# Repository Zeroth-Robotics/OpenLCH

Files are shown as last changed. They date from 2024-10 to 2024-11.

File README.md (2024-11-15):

<div align="center" style="text-align: center;">

  <h1>Zeroth Bot</h1>  (WIP)

<p> Super hackable, affordable, and end-to-end (sim2real, RL) 3D-printed open-source humanoid robot platform. Fully open-source, including hardware, SDK, and sim environments. BoM starts at $350. </p>

<p> This project is built by the open-source community and is currently work in progress. We welcome your feedback, issues, and pull requests in GitHub or joining our <a href="https://discord.gg/G6KP76uha5">Discord</a>. </p>

<h3>
  <a href="https://docs.zeroth.bot">Docs</a>
  <span> · </span>
  <a href="https://docs.zeroth.bot/roadmap">Roadmap</a>
  <span> · </span>
  <a href="https://discord.gg/G6KP76uha5">Contribute</a>
  <span> · </span>
  <a href="https://discord.gg/G6KP76uha5">Community</a>
</h3>

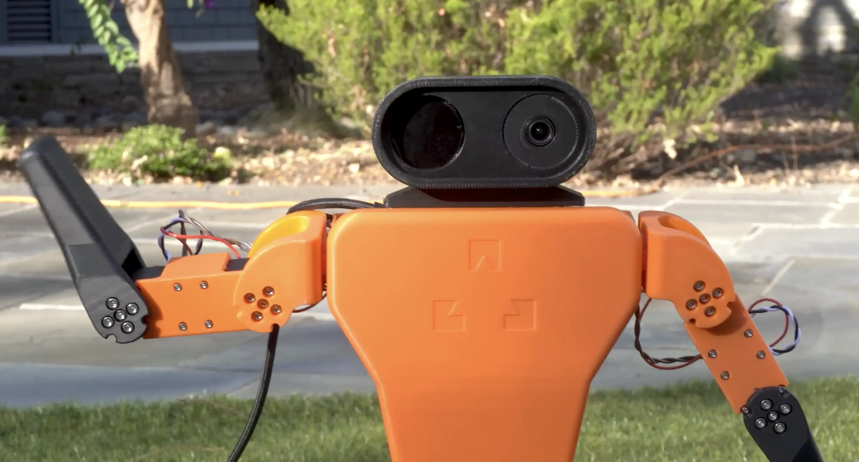
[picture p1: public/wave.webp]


</div>

---
### Project Status
Public Alpha. Zeroth-01 Bot is available for basic locomotion, vision, and speech, but expect breaking changes until 1.0 is reached.

### To start using Zeroth Bot
- Please see the Getting Started documentation at [https://docs.zeroth.bot](https://docs.zeroth.bot).

### To start developing Zeroth Bot
Zeroth Bot is developed by the open-source community. We welcome both pull requests and issues on GitHub.

- Join the community [Discord](https://discord.gg/G6KP76uha5)
- Documentation at [https://docs.zeroth.bot](https://docs.zeroth.bot)

### License
This project is licensed under the MIT License.

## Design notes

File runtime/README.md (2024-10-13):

# Runtime Documentation

## Setup

1. Flash the Image to the SD Card
Download the OpenLCH image from the [releases page](https://github.com/Zeroth-Robotics/OpenLCH-buildroot/releases).

Use Balena Etcher (or any other flashing tool) to flash the image onto your SD card.

Once flashing is complete, remove and reinsert the SD card into your computer.

3. Configure Wi-Fi on Startup
Open the boot folder on the SD card (it should be visible on macOS since it is formatted as FAT32).
Create a new file named wpa_supplicant.conf in the boot folder and add the following content:

```bash
ctrl_interface=/var/run/wpa_supplicant
ap_scan=1
update_config=1

network={
  ssid="YOURWIFINAME"
  psk="YOURPASSWORD"
  key_mgmt=WPA-PSK
}
```
Replace YOURWIFINAME and YOURPASSWORD with your Wi-Fi credentials.

3. Connect via USB
If you're connecting via USB, use the following details:

- IP Address: 192.168.42.1
- Username: root
- Password: milkv

SSH:
`ssh root@192.168.42.1`

4. Build Runtime
```bash
cargo check && gitlab-ci-local # check and build
```

5. Transfer Files to the Target Device
Find binaries in target/riscv64gc-unknown-linux-musl/release/

`scp -O target/riscv64gc-unknown-linux-musl/release/runtime $MILKV_IP:/usr/local/bin/`

Debug:
Note that you cannot ping the device in Cursor editor terminal for some reason. Try:
```bash
ping 192.168.42.1
```

6. Run the Application
To run the servo setup, execute the following on the target device:

```bash

# List available binaries
ls /usr/local/bin/

# Run your desired binary (example: runtime)
 /usr/local/bin/runtime
```

If the board is connected over usb, ip is `192.168.42.1`

---

## Architecture

Runtime Architecture

The goal of the runtime is to provide a unified interface for:

- robot configuration and declaration
- control loop execution
- state management
- model inference
- error handling and safety

## `config/[robot-name].toml`

Define the robot: joints, servos, parameters, etc.

Based on robot from `kscalelabs/firmware` config.

## `robot.rs`

Create the robot struct based on the config.toml file with all the servos and joints.

Provides the states for the robot.

Based on robot from `kscalelabs/firmware` Robot struct.

## `hal.rs`

Servo control code

## `controller.rs`

`StandingControllerPID` -> controller for standing using pre-set positions and PID controller

`StandingControllerPPO` -> controller for standing using PPO model

## `model.rs`

onnx inference session and initalization.

## `main.rs`

initialize config, robot, controller and start standing using controller.

# Hardware
Servo ID:


Wiring:


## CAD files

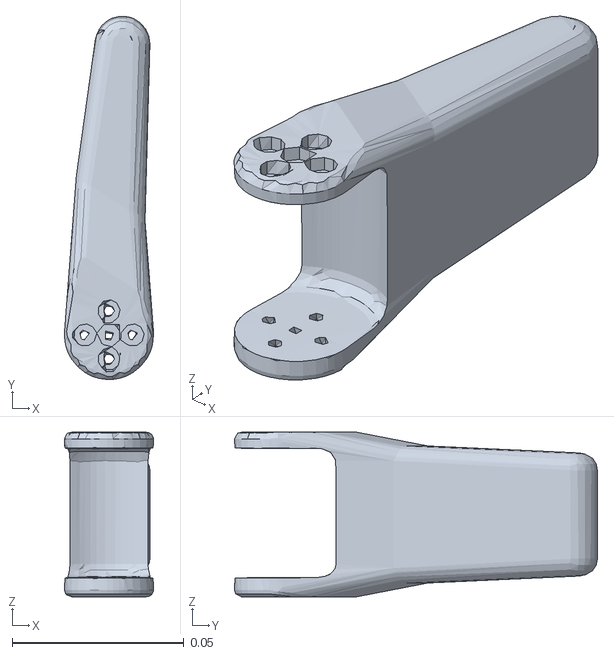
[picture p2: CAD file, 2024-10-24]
experiments/teleop/urdf/meshes/Left_Hand.stl
0.0259 x 0.106 x 0.048

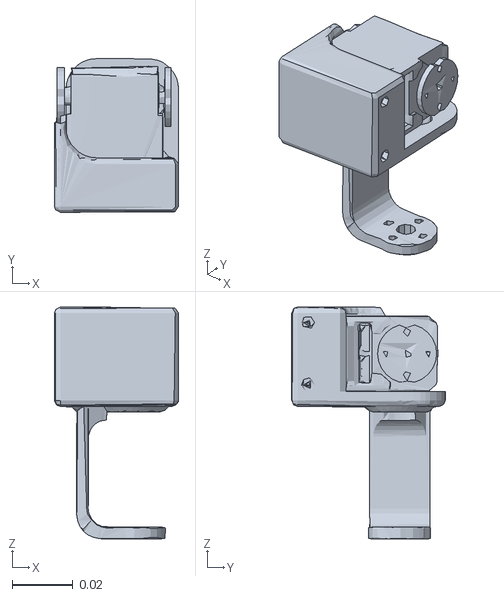
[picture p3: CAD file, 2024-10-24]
experiments/teleop/urdf/meshes/hip_yaw_right.stl
0.041 x 0.0507 x 0.0766

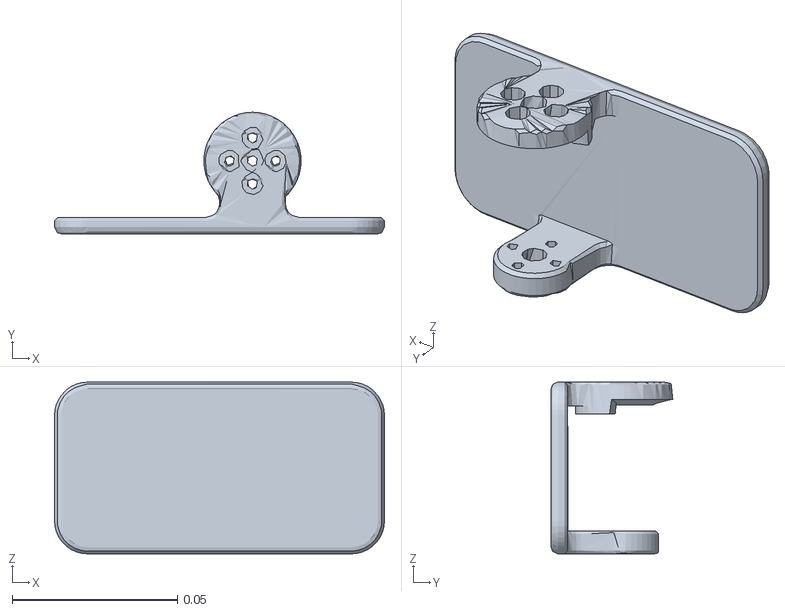
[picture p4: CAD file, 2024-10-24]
experiments/teleop/urdf/meshes/foot_right.stl
0.1 x 0.0369 x 0.0521

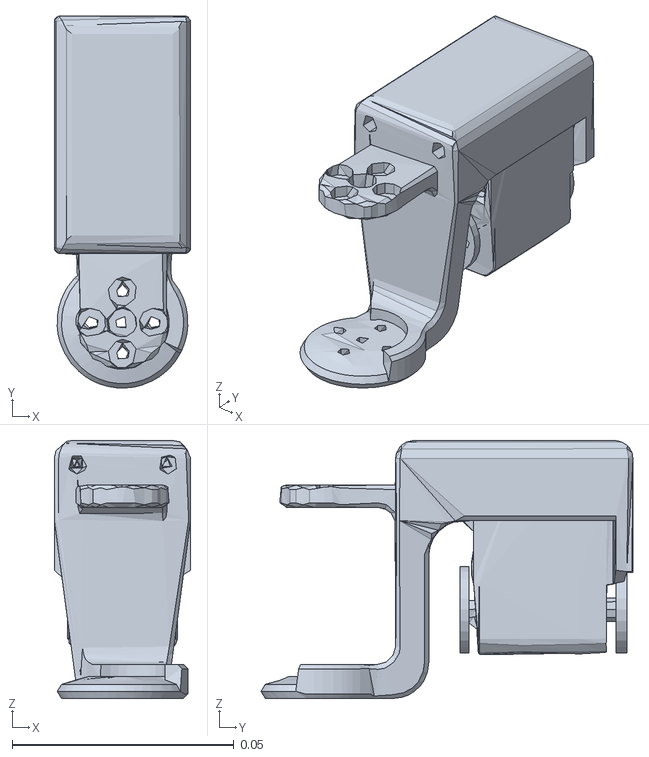
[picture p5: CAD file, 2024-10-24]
experiments/teleop/urdf/meshes/hip_roll_right.stl
0.0307 x 0.0838 x 0.0581

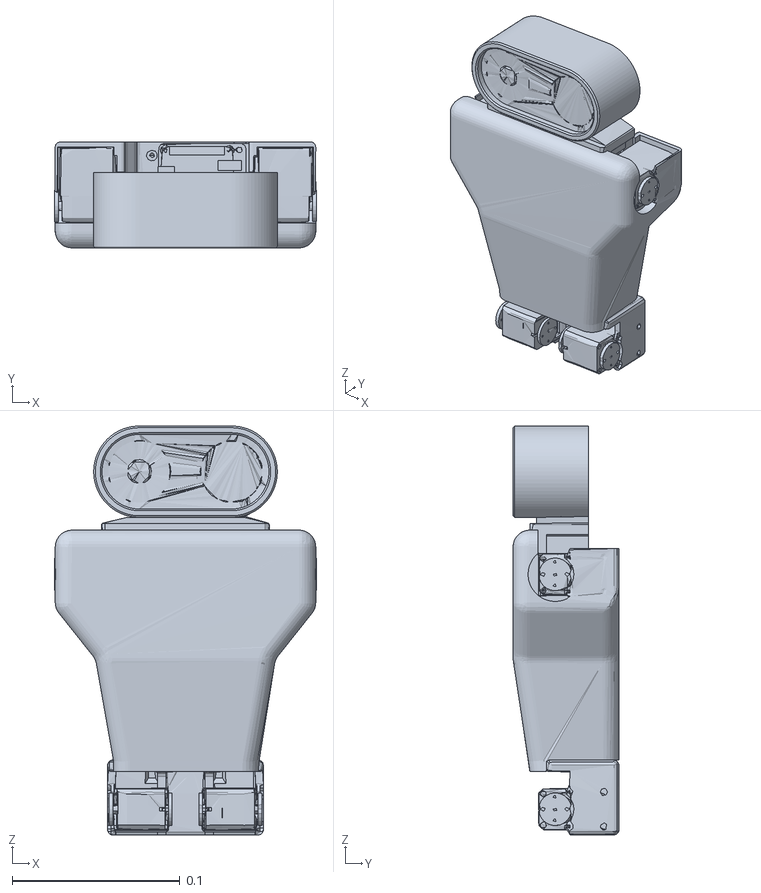
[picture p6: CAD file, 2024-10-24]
experiments/teleop/urdf/meshes/Torso.stl
0.156 x 0.0633 x 0.244

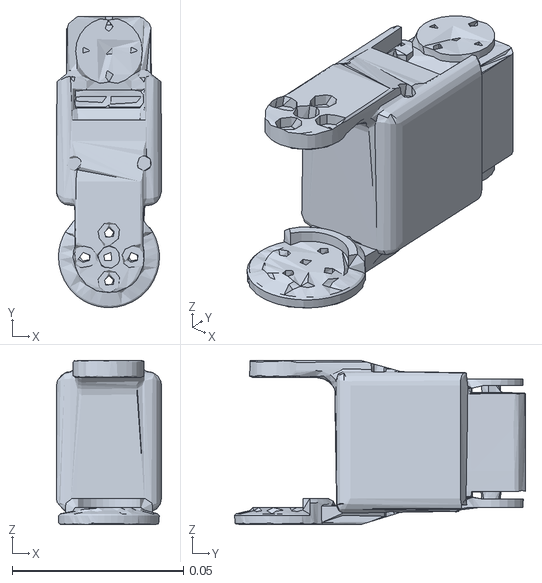
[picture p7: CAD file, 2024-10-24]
experiments/teleop/urdf/meshes/ankle_pitch_right.stl
0.0307 x 0.0851 x 0.048

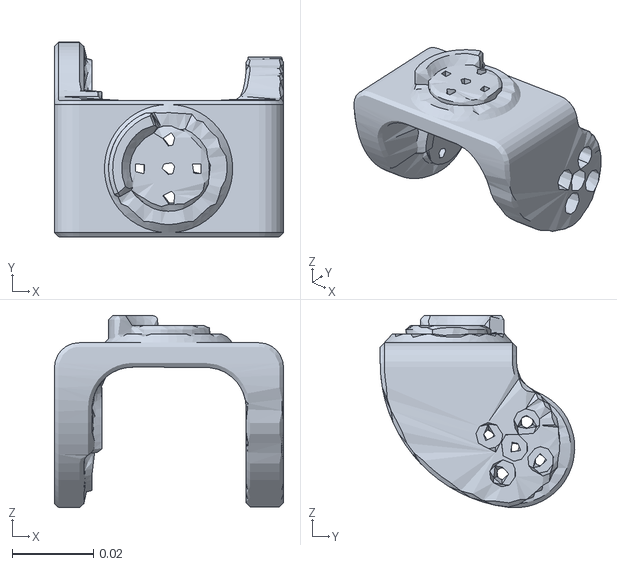
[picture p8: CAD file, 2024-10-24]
experiments/teleop/urdf/meshes/shoulder_yaw_left.stl
0.0562 x 0.0478 x 0.0472

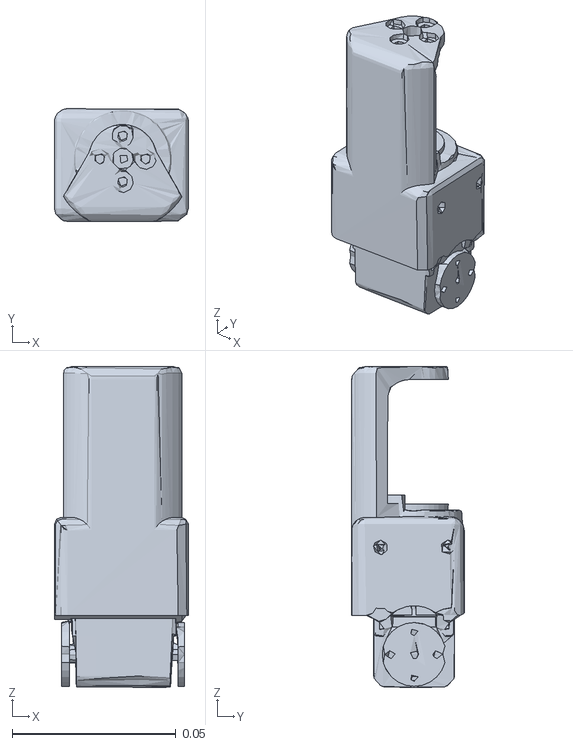
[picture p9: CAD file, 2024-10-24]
experiments/teleop/urdf/meshes/knee_pitch_right_2.stl
0.041 x 0.0345 x 0.0981

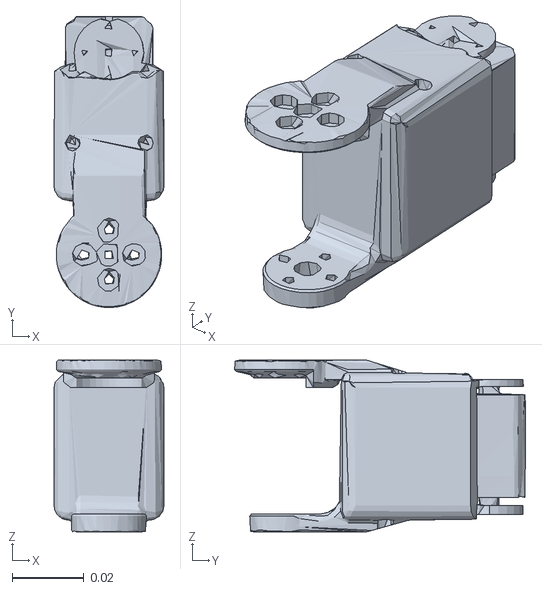
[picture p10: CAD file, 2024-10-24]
experiments/teleop/urdf/meshes/ankle_pitch_left.stl
0.0307 x 0.0813 x 0.048

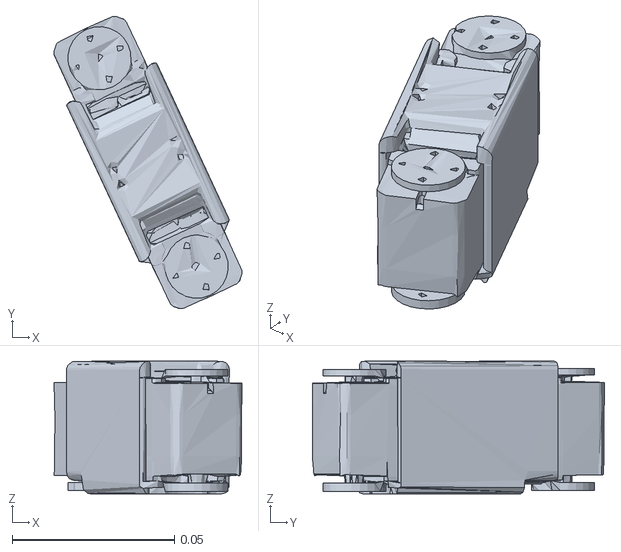
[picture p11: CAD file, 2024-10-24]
experiments/teleop/urdf/meshes/right_shoulder_yaw_motor.stl
0.058 x 0.0902 x 0.041

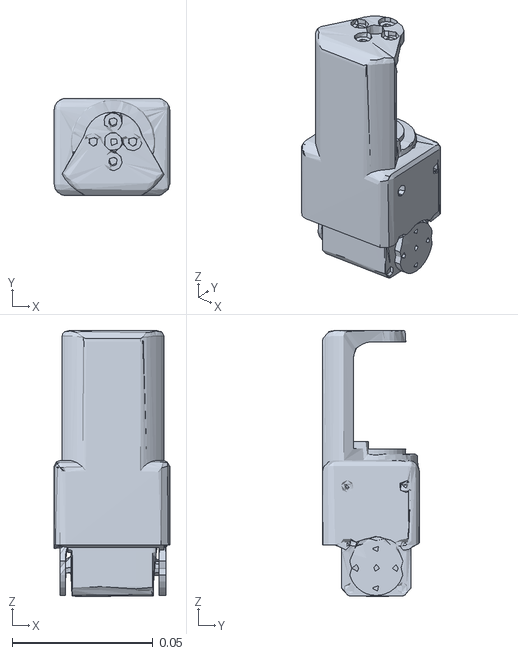
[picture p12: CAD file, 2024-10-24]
experiments/teleop/urdf/meshes/knee_pitch_right.stl
0.041 x 0.0345 x 0.0944

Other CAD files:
experiments/teleop/urdf/meshes/foot_left.stl
experiments/teleop/urdf/meshes/hip_roll_left.stl
experiments/teleop/urdf/meshes/hip_yaw_left.stl
experiments/teleop/urdf/meshes/hand_right.stl
experiments/teleop/urdf/meshes/shoulder_yaw_right.stl
experiments/teleop/urdf/meshes/left_shoulder_yaw_motor.stl

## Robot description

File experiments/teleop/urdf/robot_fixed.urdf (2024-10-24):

<robot name="opus">
  <link name="base">
    <inertial>
      <origin rpy="0 0 0" xyz="0 0 0" />
      <mass value="0.001" />
      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
    </inertial>
  </link>
  <joint name="floating_base" type="fixed">
    <origin rpy="0 0 0" xyz="0 0 0" />
    <parent link="base" />
    <child link="Torso" />
  </joint>
  <link name="Torso">
    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
    <inertial>
      <mass value="1.5697539312" />
      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
      <origin xyz="0.0006379977765356807 0.0037125891477163145 -0.0018039549717621631" rpy="0 0 0" />
    </inertial>
  </link>
  <joint name="right_shoulder_pitch" type="revolute">
    <origin xyz="-0.07813646375169968 -0.0003355559182753147 0.04305328991827533" rpy="1.5707963 2.220446049250313e-16 1.5707963" />
    <parent link="Torso" />
    <child link="shoulder_yaw_right" />
    <limit effort="1" velocity="20" lower="-1.5707963" upper="1.5707963" />
    <axis xyz="0 0 1" />
  </joint>
  <link name="shoulder_yaw_right">
    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
    <inertial>
      <mass value="0.040362728" />
      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
      <origin xyz="-0.00037600968 -0.0036566476 -0.017432914" rpy="0 0 0" />
    </inertial>
  </link>
  <joint name="left_shoulder_pitch" type="revolute">
    <origin xyz="0.0781635406483003 -0.0003355560817246521 0.04305329008172466" rpy="-1.5707963071795865 0.0 1.5707963000000003" />
    <parent link="Torso" />
    <child link="shoulder_yaw_left" />
    <limit effort="1" velocity="20" lower="-1.5707963" upper="1.5707963" />
    <axis xyz="0 0 1" />
  </joint>
  <link name="shoulder_yaw_left">
    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
    <inertial>
      <mass value="0.040363129" />
      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
      <origin xyz="-0.00037590896 0.0036565205 -0.017432695" rpy="0 0 0" />
    </inertial>
  </link>
  <joint name="right_shoulder_yaw" type="revolute">
    <origin xyz="-0.018825 -0.01629921 -0.03" rpy="3.1415927 -1.5707963 0" />
    <parent link="shoulder_yaw_right" />
    <child link="right_shoulder_yaw_motor" />
    <limit effort="1" velocity="20" lower="-1.5707963" upper="1.5707963" />
    <axis xyz="0 0 -1" />
  </joint>
  <link name="right_shoulder_yaw_motor">
    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
    <inertial>
      <mass value="0.17145988099999998" />
      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
      <origin xyz="-0.014954779548987598 0.03207058001285851 0.01810151127113155" rpy="0 0 0" />
    </inertial>
  </link>
  <joint name="right_hip_pitch" type="revolute">
    <origin xyz="-0.04563646320240432 -0.00033555485567163604 -0.09694671547403086" rpy="-1.570796353589792 -4.6410206566704915e-08 1.5707963000000003" />
    <parent link="Torso" />
    <child link="hip_yaw_right" />
    <limit effort="1" velocity="20" lower="-1.5707963" upper="1.5707963" />
    <axis xyz="0 0 -1" />
  </joint>
  <link name="hip_yaw_right">
    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
    <inertial>
      <mass value="0.10319577099999999" />
      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
      <origin xyz="-0.007775213144040673 -0.010188892005385952 0.015272495649744542" rpy="0 0 0" />
    </inertial>
  </link>
  <joint name="left_hip_pitch" type="revolute">
    <origin xyz="0.04566353964830031 -0.0003355550191209561 -0.09694671547403086" rpy="1.5707963535897942 -4.6410206566704915e-08 1.5707963000000003" />
    <parent link="Torso" />
    <child link="hip_yaw_left" />
    <limit effort="1" velocity="20" lower="-1.5707963" upper="1.5707963" />
    <axis xyz="0 0 -1" />
  </joint>
  <link name="hip_yaw_left">
    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
    <inertial>
      <mass value="0.103201904" />
      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
      <origin xyz="-0.007776157110492239 0.010188687432665504 0.015271760814946028" rpy="0 0 0" />
    </inertial>
  </link>
  <joint name="left_shoulder_yaw" type="revolute">
    <origin xyz="-0.018825 0.01629921 -0.03" rpy="3.1415927 1.5707963 0" />
    <parent link="shoulder_yaw_left" />
    <child link="left_shoulder_yaw_motor" />
    <limit effort="1" velocity="20" lower="-1.5707963" upper="1.5707963" />
    <axis xyz="0 0 1" />
  </joint>
  <link name="left_shoulder_yaw_motor">
    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
    <inertial>
      <mass value="0.171459652" />
      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
      <origin xyz="0.01495475586438801 -0.03207058301892832 -0.018101540546377845" rpy="0 0 0" />
    </inertial>
  </link>
  <joint name="right_hip_yaw" type="revolute">
    <origin xyz="-0.02550000162875169 0.0025000011415515153 0.019359999918275368" rpy="9.282041333256968e-08 1.5707963000000005 0.0" />
    <parent link="hip_yaw_right" />
    <child link="hip_roll_right" />
    <limit effort="1" velocity="20" lower="-0.087266463" upper="1.5707963" />
    <axis xyz="0 0 1" />
  </joint>
  <link name="hip_roll_right">
    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
    <inertial>
      <mass value="0.111293388" />
      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
      <origin xyz="5.2211227247596255e-05 0.04271834544407224 0.027962543113983985" rpy="0 0 0" />
    </inertial>
  </link>
  <joint name="left_hip_yaw" type="revolute">
    <origin xyz="-0.02550000297464769 -0.0025000010000000017 0.01936000008172467" rpy="-3.1415926071795863 -1.5707963 0.0" />
    <parent link="hip_yaw_left" />
    <child link="hip_roll_left" />
    <limit effort="1" velocity="20" lower="-1.5707963" upper="0.087266463" />
    <axis xyz="0 0 1" />
  </joint>
  <link name="hip_roll_left">
    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
    <inertial>
      <mass value="0.111293526" />
      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
      <origin xyz="-5.2212826152564546e-05 0.04271835909112089 0.027962565619545642" rpy="0 0 0" />
    </inertial>
  </link>
  <joint name="right_elbow_yaw" type="revolute">
    <origin xyz="-0.03000311610855749 0.06434189253104221 0.00025000101875458525" rpy="8.847213864293657e-08 -1.9613800805728943e-08 0.4363323099999996" />
    <parent link="right_shoulder_yaw_motor" />
    <child link="Left_Hand" />
    <limit effort="1" velocity="20" lower="-1.2217305" upper="1.2217305" />
    <axis xyz="0 0 1" />
  </joint>
  <link name="Left_Hand">
    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
    <inertial>
      <mass value="0.075184887" />
      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
      <origin xyz="0.0011184952 0.046132358 0.018254412" rpy="0 0 0" />
    </inertial>
  </link>
  <joint name="left_elbow_yaw" type="revolute">
    <origin xyz="0.03000311710160605 -0.06434189183411612 -0.0002500013458960012" rpy="-3.141592607179586 -2.220446049250313e-16 0.43633231000000006" />
    <parent link="left_shoulder_yaw_motor" />
    <child link="hand_right" />
    <limit effort="1" velocity="20" lower="-1.2217305" upper="1.2217305" />
    <axis xyz="0 0 1" />
  </joint>
  <link name="hand_right">
    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
    <inertial>
      <mass value="0.075183656" />
      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
      <origin xyz="-0.0011185716 0.046132566 0.018254616" rpy="0 0 0" />
    </inertial>
  </link>
  <joint name="right_hip_roll" type="revolute">
    <origin xyz="0.0 0.06776001387753285 0.015000000939161373" rpy="1.5707963999999996 0.0 0.0" />
    <parent link="hip_roll_right" />
    <child link="knee_pitch_right" />
    <limit effort="1" velocity="20" lower="-0.78539816" upper="0.78539816" />
    <axis xyz="0 0 1" />
  </joint>
  <link name="knee_pitch_right">
    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
    <inertial>
      <mass value="0.11061241299999999" />
      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
      <origin xyz="0.0007189519537218518 -0.0023746643916922137 -0.021913106490424647" rpy="0 0 0" />
    </inertial>
  </link>
  <joint name="left_hip_roll" type="revolute">
    <origin xyz="0.0 0.06776001212246713 0.014999999060838654" rpy="1.5707963 0.0 0.0" />
    <parent link="hip_roll_left" />
    <child link="knee_pitch_right_2" />
    <limit effort="1" velocity="20" lower="-0.78539816" upper="0.78539816" />
    <axis xyz="0 0 1" />
  </joint>
  <link name="knee_pitch_right_2">
    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
    <inertial>
      <mass value="0.11061241299999999" />
      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
      <origin xyz="-0.0006438206184322414 -0.0023746644421732206 -0.024438821233669406" rpy="0 0 0" />
    </inertial>
  </link>
  <joint name="right_knee_pitch" type="revolute">
    <origin xyz="0.01882501239711481 -9.39161338975314e-10 -0.04221000153916135" rpy="-1.5707963 0.0 1.5707963" />
    <parent link="knee_pitch_right" />
    <child link="ankle_pitch_right" />
    <limit effort="1" velocity="20" lower="-1.0471976" upper="1.0471976" />
    <axis xyz="0 0 1" />
  </joint>
  <link name="ankle_pitch_right">
    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
    <inertial>
      <mass value="0.109625116" />
      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
      <origin xyz="-5.290268857115649e-07 0.04092239693101483 0.017864163896558594" rpy="0 0 0" />
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

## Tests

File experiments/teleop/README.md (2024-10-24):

# Teleop (WIP)

Documentation link: https://docs.zeroth.bot/software/teleop

Objective: Control the robot using a GUI by setting target positions for the hands or using VR controllers.

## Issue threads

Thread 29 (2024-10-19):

python lib set_positions sets all the positions, not just the specified one

npfoss, 2024-10-19:
using this function as a wrapper fixes it, but the underlying bug is in the rust code (never updates `last_positions`, we think?)

```py
def set_one(id, position):
    current_pos = hal.servo.get_positions()
    updated_pos = [(servo_id, position if servo_id == id else pos) for servo_id, pos in current_pos]
    print('setting', updated_pos)
    hal.servo.set_positions(updated_pos)
```

hatomist, 2024-10-22:
should be fixed by
https://github.com/Zeroth-Robotics/OpenLCH/commit/ddc89fab7815edb4a0c2348b4526b904a46f3129

Closed 2024-10-22.

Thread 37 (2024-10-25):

Fix `openlch start-calibration #` id setting permanence

jingxiangmo, 2024-10-25:
Currently not consistent

hatomist, 2024-10-29:
should be fixed by v0.2.3 of image

Closed 2024-10-29.

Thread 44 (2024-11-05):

Calibration doesn't save min/max results

jingxiangmo, 2024-11-05:

jingxiangmo, 2024-11-05:
issue noted two days ago. After setting the robot to calibrate, the calibrated value didn't save.

Closed 2024-11-08.

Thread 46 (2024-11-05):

Sending all servos to 0s after calibration issue

jingxiangmo, 2024-11-05:
Change cables?

jingxiangmo, 2024-11-05:
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

Closed 2024-11-08.

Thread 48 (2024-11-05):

Electromagnetic interference (EMI) from cables to servo

jingxiangmo, 2024-11-05:
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

jingxiangmo, 2024-11-05:
i suspect it's the longer cables. can we can new cables made in China or etc. EMI would mess with the policy input

Closed 2024-11-08.

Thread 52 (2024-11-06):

openlch 0.9.0 issues

jingxiangmo, 2024-11-06:

jingxiangmo, 2024-11-07:
- `openlch set-position [joint id] [position]` does not set servo positions
- read_servos_id missing #16

jingxiangmo, 2024-11-07:
```
(openlch) ➜  inference git:(walked) ✗ openlch scan-servos
Found servo IDs:
1
2
3
4
5
6
7
8
9
10
11
12
13
14
15
(openlch) ➜  inference git:(walked) ✗ openlch set-position 16 40
```

Closed 2024-11-08.

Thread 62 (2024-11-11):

Add visual command arrow to sim visualization

henri123lemoine, 2024-11-11:
The simulation needs a visual indicator (green arrow) showing the commanded direction/velocity of the robot. E.g. visual linear velocity commands (x,y) and angular velocity/heading commands.

henri123lemoine, 2024-11-11:
(wrong repo)

henri123lemoine, 2024-11-11:
(wrong repo)

henri123lemoine, 2024-11-11:
(wrong repo)

Closed 2024-11-11.

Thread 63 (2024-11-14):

`start-calibration` doesn't start unless cancel first with new image

jingxiangmo, 2024-11-14:

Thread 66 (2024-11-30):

Does zeroth-bot have gazebo emulation robots,Thinks.

runkezhong, 2024-11-30:

jingxiangmo, 2024-11-30:
The bot has a URDF  file that defines link and joints (, which we use in Isaac Gym. You can convert the URDF to SDF (Gazebo compatible format) using a converter like `gz sdf`

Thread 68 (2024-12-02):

Switch submodule connection from SSH to HTTPS

henri123lemoine, 2024-12-02:
In `.gitmodules`, "sim" submodule URL switch from `git@github.com:Zeroth-Robotics/sim.git` to `https://github.com/zeroth-robotics/sim.git`. I'm not entirely sure that would fix the issue with `--recurse-submodules` cloning of zeroth-bot, but don't see why it wouldn't.

Closed 2025-05-24.

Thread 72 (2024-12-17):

The price of sts3250 is actually 80.15

GoingMyWay, 2024-12-17:
https://www.aliexpress.us/item/3256806337383027.html?gatewayAdapt=glo2usa4itemAdapt

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

The price of sts3250 is actually 80.15

On Taobao.com the price is RMB 464.

lijiajun3029, 2024-12-25:
I think this is very expensive.

jingxiangmo, 2024-12-25:
Yeah the seller has significantly increased the cost of STS3250s... We're getting new custom STS3215s with high RPMs made right now

GoingMyWay, 2024-12-26:
> Yeah the seller has significantly increased the cost of STS3250s... We're getting new custom STS3215s with high RPMs made right now

Do you mean the price of it was low?

jingxiangmo, 2024-12-26:
Yup, 3215 was $11 and 3250 was $30. We originally started with 3215, but 3250's performance was better because of the higher RPM so we changed the BoM for 3250 as we're getting custom servos made by new suppliers right now that would be 3215 price but 65 RPM

lijiajun3029, 2024-12-27:
> Yup, 3215 was $11 and 3250 was $30. We originally started with 3215, but 3250's performance was better because of the higher RPM so we changed the BoM for 3250 as we're getting custom servos made by new suppliers right now that would be 3215 price but 65 RPM

Further consider how much torque and rpm we need in different parts(legs and hands) of the robot？some sts3215 have 19.5kg@7.4v torque and 52rpm@7.4v(but our battery is 12v)

Closed 2024-12-25.

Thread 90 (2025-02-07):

Something wrong with environmental issues and a value bug of run.py

BitBelief, 2025-02-07:
**wrong message:**
(humanoid-os) **user@user-System-Product-Name:~/zeroth-bot$** python experiments/run.py
pygame 2.6.1 (SDL 2.28.4, Python 3.12.8)
Hello from the pygame community. https://www.pygame.org/contribute.html
INFO:robot:Robot initializing...
INFO:robot:Checking connection to robot...
INFO:robot:Successfully pinged robot.
INFO:robot:Scanning servos...
Error during robot operation: <_InactiveRpcError of RPC that terminated with:
	status = StatusCode.UNIMPLEMENTED
	details = ""
	debug_error_string = "UNKNOWN:Error received from peer  {grpc_message:"", grpc_status:12, created_time:"2025-02-06T17:10:41.2711877+08:00"}"
>
Traceback (most recent call last):
  File "/home/user/zeroth-bot/experiments/run.py", line 478, in <module>
    main()
  File "/home/user/zeroth-bot/experiments/run.py", line 468, in main
    stop_event.set()
    ^^^^^^^^^^
UnboundLocalError: cannot access local variable 'stop_event' where it is not associated with a value

**anotherone(about video-stream service):**
(humanoid-os) <font color="#4E9A06"><b>user@user-System-Product-Name</b></font>:<font color="#3465A4"><b>~/zeroth-bot</b></font>$ openlch start-video-stream
An error occurred: <_InactiveRpcError of RPC that terminated with:
	status = StatusCode.UNIMPLEMENTED
	details = ""
	debug_error_string = "UNKNOWN:Error received from peer  {grpc_message:"", grpc_status:12, created_time:"2025-02-06T17:10:18.204871362+08:00"}"
>

mrking66, 2025-03-22:
hey,have you been solved this problem?I have the same problem,too.It seems to be a gRPC error, and I'm not sure if the server has implemented the method called by the client.

BitBelief, 2025-04-11:
I'm sorry to tell you that I still haven't found a solution.If I find a solution I will leave a message on it.

Closed 2025-05-24.

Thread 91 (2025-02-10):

Docs don't show how to initialize the robot

fruit-lxe, 2025-02-10:
How to initialize the robot to ensure that it is in the same position every time it is powered on, so that subsequent actions can be performed?

Mysticwaan, 2025-03-09:
Use a limit switch, encoder, or preset servo position to the robot on startup @fruit-lxe

jingxiangmo, 2025-03-15:
There's a calibration script that goes to max and minimum positions, and then the zero position is the half

jingxiangmo, 2025-03-15:
Thanks, I will update the docs

Closed 2025-05-24.

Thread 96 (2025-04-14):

The link in the "ID and calibration" has expired.

Kyaru-Momochi, 2025-04-14:
It show me error code: 502

Closed 2025-05-24.

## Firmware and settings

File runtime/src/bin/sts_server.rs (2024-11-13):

use tonic::{transport::Server, Request, Response, Status};
use tower_http::cors::CorsLayer;
use std::sync::Arc;
use tokio::sync::Mutex;
use anyhow::Result;
use std::fs::File;
use std::io::Write;
use std::path::Path;
use std::process::{Command, Stdio};
use std::net::IpAddr;
use regex::Regex;
use std::sync::atomic::{AtomicBool, Ordering};
use tokio::task;
use std::time::Duration;
use std::env;
use runtime::hal::{Servo, IMU, MAX_SERVOS, ServoMultipleWriteCommand, ServoData, ServoMode, ServoDirection, ServoRegister, TorqueMode};
use std::collections::HashMap;
use tokio::sync::RwLock;
use uuid::Uuid;
use tokio::fs;
use std::path::PathBuf;
use std::pin::Pin;
use chrono::prelude::*;
use tokio_stream::{self, StreamExt, Stream};

pub mod servo_control {
    tonic::include_proto!("hal_pb");
}

use servo_control::servo_control_server::{ServoControl, ServoControlServer};
use servo_control::{Empty, JointPositions, WifiCredentials, ServoId, ServoInfo, ServoIds, IdChange, ChangeIdResponse, ServoInfoResponse, servo_info_response, change_id_response, VideoStreamUrls, CalibrationResponse, CalibrationStatus, TorqueSettings, TorqueEnableSettings, ImuData, Vector3, AudioChunk, UploadResponse, PlayRequest, RecordingConfig, CalibrationRequest};

#[derive(Debug)]
pub struct StsServoControl {
    servo: Arc<Mutex<Servo>>,
    imu: Arc<Mutex<Option<IMU>>>,
    last_positions: Arc<Mutex<ServoData>>,
    calibrating_servo: Arc<Mutex<Option<u8>>>,
    calibration_running: Arc<AtomicBool>,
    audio_files: Arc<RwLock<HashMap<String, PathBuf>>>,
    recording_running: Arc<AtomicBool>,
}

impl StsServoControl {
    pub fn new() -> Result<Self> {
        let servo = Servo::new()?;
        let imu = IMU::new().ok();
        servo.enable_readout()?;
        let initial_data = servo.read_continuous()?;
        
        Ok(Self {
            servo: Arc::new(Mutex::new(servo)),
            imu: Arc::new(Mutex::new(imu)),
            last_positions: Arc::new(Mutex::new(initial_data)),
            calibrating_servo: Arc::new(Mutex::new(None)),
            calibration_running: Arc::new(AtomicBool::new(false)),
            audio_files: Arc::new(RwLock::new(HashMap::new())),
            recording_running: Arc::new(AtomicBool::new(false)),
        })
    }

    fn get_interface_ip(interface: &str) -> Option<IpAddr> {
        let output = Command::new("ip")
            .args(&["addr", "show", interface])
            .output()
            .ok()?;
        
        let output_str = String::from_utf8_lossy(&output.stdout);
        let ip_regex = Regex::new(r"inet\s+(\d+\.\d+\.\d+\.\d+)").ok()?;
        
        ip_regex.captures(&output_str)
            .and_then(|cap| cap.get(1))
            .and_then(|m| m.as_str().parse().ok())
    }

    async fn calibrate_servo(&self, servo_id: u8, calibration_speed: u16, current_threshold: f32) -> Result<(), Status> {
        let servo = self.servo.clone();
        let calibrating_servo = self.calibrating_servo.clone();
        let calibration_running = self.calibration_running.clone();

        task::spawn(async move {
            let servo = servo.lock().await;

            servo.disable_movement().unwrap();


            servo.disable_readout().unwrap();
            servo.set_mode(servo_id, ServoMode::ConstantSpeed).unwrap();

            servo.write_servo_memory(servo_id, runtime::hal::ServoRegister::TorqueLimit, 150).unwrap();

            let mut max_forward = 0;
            let mut max_backward = 0;

            let version = servo.read(servo_id, ServoRegister::ServoMainVersion, 2).unwrap();
            let mut current_multiplier = 1.0;

            // sts3215
            if version[0] == 0x09 && version[1] == 0x03 {
                current_multiplier = 6.5;
            }

            for pass in 0..2 {
                let direction = if pass == 0 { ServoDirection::Clockwise } else { ServoDirection::Counterclockwise };
                servo.set_speed(servo_id, calibration_speed, direction).unwrap();

                let mut threshold_exceeded_count = 0;

                loop {
                    if !calibration_running.load(Ordering::SeqCst) {
                        servo.set_speed(servo_id, 0, ServoDirection::Clockwise).unwrap();
                        return;
                    }

                    let mut info = servo.read_info(servo_id).unwrap();
                    let mut retry_count = 0;
                    while info.current_current == 0 && info.current_location == 0 && retry_count < 3 {
                        tokio::time::sleep(Duration::from_millis(1)).await;
                        info = servo.read_info(servo_id).unwrap();
                        retry_count += 1;
                    }
                    let position = info.current_location;
                    let current = info.current_current as f32 * 6.5 / 100.0 * current_multiplier;
                    
                    if current > current_threshold {
                        threshold_exceeded_count += 1;
                        
                        if threshold_exceeded_count >= 3 {
                            for _ in 0..3 { 
                                tokio::time::sleep(Duration::from_millis(10)).await;
                                servo.set_speed(servo_id, 0, direction).unwrap();
                            }
                            tokio::time::sleep(Duration::from_millis(100)).await;

                            servo.set_speed(servo_id, calibration_speed, opposite_direction(direction)).unwrap();
                            tokio::time::sleep(Duration::from_millis(350)).await;

                            servo.set_speed(servo_id, 0, opposite_direction(direction)).unwrap();
                            tokio::time::sleep(Duration::from_millis(100)).await;

                            let info = servo.read_info(servo_id).unwrap();

                            if direction == ServoDirection::Clockwise {
                                max_forward = info.current_location;
                            } else {
                                max_backward = info.current_location;
                            }

                            break;
                        }
                    } else {
                        threshold_exceeded_count = 0;
                    }

                    tokio::time::sleep(Duration::from_millis(10)).await;
                }

                if pass < 1 {
                    tokio::time::sleep(Duration::from_millis(500)).await;
                }
            }

            servo.write(servo_id, ServoRegister::LockMark, &[0]).unwrap();
            servo.set_speed(servo_id, 0, ServoDirection::Clockwise).unwrap();
            servo.write_servo_memory(servo_id, ServoRegister::TorqueLimit, 600).unwrap();
            servo.set_mode(servo_id, ServoMode::Position).unwrap();
            servo.write(servo_id, ServoRegister::LockMark, &[1]).unwrap();

            servo.enable_readout().unwrap();
            *calibrating_servo.lock().await = None;
            calibration_running.store(false, Ordering::SeqCst);
            Self::calculate_and_write_calibration(servo_id, &servo, max_backward, max_forward).await.unwrap();
        });

        Ok(())
    }

    async fn calculate_and_write_calibration(servo_id: u8, servo: &Servo, min_pos: i16, max_pos: i16) -> Result<(), Status> {
        let mut max_pos = max_pos;

        if max_pos < min_pos {
            max_pos += 4096;
        }
    
        let offset_value = min_pos + (max_pos - min_pos) / 2 - 2048;
    
        // Convert offset to 12-bit signed value
        let offset_value = if offset_value < 0 {
            offset_value.abs() as u16 | 0x800 // (set negative bit)
        } else {
            if offset_value > 2048 {
                (offset_value - 4096).abs() as u16 | 0x800
            } else {
                offset_value as u16
            }
        };
    
        // Calculate new limits
        let min_angle = 2048 - (max_pos - min_pos) / 2;
        let max_angle = 2048 + (max_pos - min_pos) / 2;

        println!("Writing calibration, offset: {}, min_angle: {}, max_angle: {}", offset_value, min_angle, max_angle);

        // Unlock EEPROM
        servo.write(servo_id, ServoRegister::LockMark, &[0])
            .map_err(|e| Status::internal(format!("Failed to unlock EEPROM: {}", e)))?;
        tokio::time::sleep(Duration::from_millis(20)).await;

        // Write new offset
        servo.write_servo_memory(servo_id, ServoRegister::PositionCorrection, offset_value)
            .map_err(|e| Status::internal(format!("Failed to write offset: {}", e)))?;
        tokio::time::sleep(Duration::from_millis(20)).await;

        // Write new limits
        for _ in 0..3 {
            servo.write_servo_memory(servo_id, ServoRegister::MinAngleLimit, min_angle as u16)
                .map_err(|e| Status::internal(format!("Failed to write MinAngleLimit: {}", e)))?;
            tokio::time::sleep(Duration::from_millis(20)).await;
            let read_min = servo.read(servo_id, ServoRegister::MinAngleLimit, 2)
                .map_err(|e| Status::internal(format!("Failed to read MinAngleLimit: {}", e)))?;
            let read_min = u16::from_le_bytes([read_min[0], read_min[1]]);
            if read_min == min_angle as u16 {
                break;
            }
        }

        for _ in 0..3 {
            servo.write_servo_memory(servo_id, ServoRegister::MaxAngleLimit, max_angle as u16)
                .map_err(|e| Status::internal(format!("Failed to write MaxAngleLimit: {}", e)))?;
            tokio::time::sleep(Duration::from_millis(20)).await;
            let read_max = servo.read(servo_id, ServoRegister::MaxAngleLimit, 2)
                .map_err(|e| Status::internal(format!("Failed to read MaxAngleLimit: {}", e)))?;
            let read_max = u16::from_le_bytes([read_max[0], read_max[1]]);
            if read_max == max_angle as u16 {
                break;
            }
        }

        // Lock EEPROM
        servo.write(servo_id, ServoRegister::LockMark, &[1])
            .map_err(|e| Status::internal(format!("Failed to lock EEPROM: {}", e)))?;

        Ok(())
    }

    fn is_process_running(process_name: &str) -> bool {
        Command::new("ps")
            .args(&["-A"])
            .stdout(Stdio::piped())
            .spawn()
            .and_then(|child| {
                let output = child.wait_with_output()?;
                Ok(String::from_utf8_lossy(&output.stdout).contains(process_name))
            })
            .unwrap_or(false)
    }

    fn start_process(process_name: &str, args: &[&str]) -> Result<(), std::io::Error> {
        Command::new(process_name)
            .args(args)
            .env("LD_LIBRARY_PATH", "/mnt/system/lib:/mnt/system/usr/lib")
            .env("PATH", "/usr/local/bin:/usr/bin:/bin:/usr/local/sbin:/usr/sbin:/sbin:/mnt/system/usr/bin:/mnt/system/usr/sbin")
            .spawn()?;
        Ok(())
    }

    fn stop_process(process_name: &str) -> Result<(), std::io::Error> {
        Command::new("pkill")
            .args(&["-SIGINT", process_name])  // Send SIGINT (Ctrl+C) signal
            .status()?;
        Ok(())
    }

    async fn save_audio_chunk(audio_id: &str, data: &[u8]) -> Result<PathBuf, Status> {
        let audio_dir = PathBuf::from("/tmp/audio");
        fs::create_dir_all(&audio_dir).await
            .map_err(|e| Status::internal(format!("Failed to create audio directory: {}", e)))?;

        let file_path = audio_dir.join(format!("{}.wav", audio_id));
        fs::write(&file_path, data).await
            .map_err(|e| Status::internal(format!("Failed to write audio file: {}", e)))?;

        Ok(file_path)
    }

    fn play_audio(file_path: &Path, volume: f32) -> Result<(), Status> {
        let _volume_db = (20.0 * volume.log10()).round() as i32;
        // let volume_arg = if volume_db <= -144 {
        //     "-M".to_string()  // Mute
        // } else {
        //     format!("-v {}", volume_db)
        // };

        Command::new("tinyplay")
            .args(&[
                file_path.to_str().unwrap(),
                "-D", "1",
                "-c", "1",
            ])
            // .arg(&volume_arg)
            .status()
            .map_err(|e| Status::internal(format!("Failed to play audio: {}", e)))?;

        Ok(())
    }
}

#[tonic::async_trait]
impl ServoControl for StsServoControl {
    async fn get_positions(&self, _request: Request<Empty>) -> Result<Response<JointPositions>, Status> {
        let servo: tokio::sync::MutexGuard<'_, Servo> = self.servo.lock().await;
        let servo_data = servo.read_continuous().map_err(|e| Status::internal(e.to_string()))?;
        
        // Update last_positions
        *self.last_positions.lock().await = servo_data.clone();
        
        let positions = JointPositions {
            positions: servo_data.servo.iter()
                .take(MAX_SERVOS)
                .enumerate()
                .map(|(id, info)| servo_control::JointPosition {
                    id: (id + 1) as i32, // Add 1 to make IDs start from 1
                    position: Servo::raw_to_degrees(info.current_location as u16),
                    speed: {
                        let speed_raw = info.current_speed as u16;
                        let speed_magnitude = speed_raw & 0x7FFF; // Remove 15th bit
                        let speed_sign = if speed_raw & 0x8000 != 0 { -1.0 } else { 1.0 };
                        speed_sign * (speed_magnitude as f32 * 360.0 / 4096.0)
                    },
                })
                .collect(),
        };
        Ok(Response::new(positions))
    }

    async fn set_positions(&self, request: Request<JointPositions>) -> Result<Response<Empty>, Status> {
        let positions = request.into_inner();
        let servo = self.servo.lock().await;
        let mut last_positions = self.last_positions.lock().await;
        let calibration_running = self.calibration_running.clone();

        if calibration_running.load(Ordering::SeqCst) {
            return Err(Status::internal("Calibration is in progress"));
        }
        
        let mut cmd = ServoMultipleWriteCommand {
            only_write_positions: 1,
            ids: [0; MAX_SERVOS],
            positions: [0; MAX_SERVOS],
            times: [0; MAX_SERVOS],
            speeds: [0; MAX_SERVOS],
        };

        for i in 0..MAX_SERVOS {
            let servo_id = (i + 1) as u32; // Add 1 because IDs start from 1
            let position = positions.positions.iter()
                .find(|p| p.id == servo_id as i32)
                .map(|p| p.position)
                .unwrap_or_else(|| Servo::raw_to_degrees(last_positions.servo[i].current_location as u16));

            cmd.ids[i] = servo_id as u8;
            cmd.positions[i] = Servo::degrees_to_raw(position) as i16;
            // You can set times and speeds here if needed
            cmd.times[i] = 0;
            cmd.speeds[i] = 0;

            last_positions.servo[i].current_location = Servo::degrees_to_raw(position) as i16;
        }

        servo.write_multiple(&cmd)
            .map_err(|e| Status::internal(e.to_string()))?;
        
        Ok(Response::new(Empty {}))
    }

    async fn set_wifi_info(&self, request: Request<WifiCredentials>) -> Result<Response<Empty>, Status> {
        println!("Got a request to set WiFi info: {:?}", request);
        let wifi_info = request.into_inner();
        
        let config_content = format!(
            "ctrl_interface=/var/run/wpa_supplicant
ap_scan=1
update_config=1
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
async fn main() -> Result<(), Box<dyn std::error::Error>> {
    let addr = "0.0.0.0:50051".parse()?;
    let servo_control = StsServoControl::new()?;

    let service = tower::ServiceBuilder::new()
        .layer(tonic_web::GrpcWebLayer::new())
        .service(ServoControlServer::new(servo_control));

    Server::builder()
        // GrpcWeb is over http1 so we must enable it.
        .accept_http1(true)
        .layer(CorsLayer::permissive())
        .add_service(service)
        .serve(addr)
        .await?;

    Ok(())
}

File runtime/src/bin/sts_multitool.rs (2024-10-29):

use anyhow::Result;
use runtime::hal::{Servo, MAX_SERVOS, TorqueMode, ServoRegister};
use cursive::views::{TextView, LinearLayout, DummyView, Panel, Dialog, EditView, SelectView};
use cursive::traits::*;
use std::sync::{Arc, Mutex};
use std::time::{Instant, Duration};
use std::sync::atomic::{AtomicI16, Ordering, AtomicBool};
use cursive::theme::{Color, ColorStyle, BaseColor};
use cursive::view::Nameable;
use std::sync::OnceLock;
use std::fs::File;
use std::io::Write;
use chrono::Local;
use serde_json::{json, Value};

static CALIBRATION_POSITION: AtomicI16 = AtomicI16::new(-1);
static CURRENT_POSITION: AtomicI16 = AtomicI16::new(0);
static CAPTURE_IN_PROGRESS: AtomicBool = AtomicBool::new(false);
static CAPTURE_STATE: OnceLock<Arc<Mutex<CaptureState>>> = OnceLock::new();

// Add this near the top of your file
static UNRESPONSIVE_SERVOS: OnceLock<Arc<Mutex<Vec<bool>>>> = OnceLock::new();

// At the top of the file, add this array of joint names
const JOINT_NAMES: [&str; 16] = [
    "R Ank", "R Knee", "R Hip R", "R Hip Y", "R Hip P",
    "L Ank", "L Knee", "L Hip R", "L Hip Y", "L Hip P",
    "R Elb", "R Sh Y", "R Sh P",
    "L Elb", "L Sh Y", "L Sh P"
];

struct CaptureState {
    file: Option<File>,
    captures: Vec<Value>,
    name: String,
}

fn show_hints(s: &mut cursive::Cursive) {
    let hints = vec![
        "Up/Down - Select servo",
        "Enter - Open servo settings",
        "T - Toggle torque",
        "[ - Start calibration",
        "] - End calibration",
        "c - Capture current position",
        "C - End and save capture",
        "Q - Quit",
        "H - Show this help",
    ];

    let content = hints.join("\n");

    s.add_layer(
        Dialog::around(TextView::new(content))
            .title("Hints")
            .button("Close", |s| { s.pop_layer(); })
    );
}

fn main() -> Result<()> {
    let servo = Arc::new(Servo::new()?);

    // Enable continuous readout
    servo.enable_readout()?;

    let mut siv = cursive::default();

    // Create a layout for our servo data
    let mut layout = LinearLayout::vertical();

    // Add header
    let header = LinearLayout::horizontal()
        .child(TextView::new("ID").center().fixed_width(4))
        .child(TextView::new("Joint").center().fixed_width(7))
        .child(TextView::new("Pos").center().fixed_width(8))
        .child(TextView::new("Spd").center().fixed_width(8))
        .child(TextView::new("Load").center().fixed_width(8))
        .child(TextView::new("Torque").center().fixed_width(8))
        .child(TextView::new("Volt").center().fixed_width(6))
        .child(TextView::new("Temp").center().fixed_width(6))
        .child(TextView::new("Curr").center().fixed_width(6))
        .child(TextView::new("Status").center().fixed_width(8))
        .child(TextView::new("Torq Lim").center().fixed_width(8));
    layout.add_child(header);

    // Add rows for each servo
    for i in 0..MAX_SERVOS {
        let joint_name = JOINT_NAMES.get(i).unwrap_or(&"Unknown");
        let row = LinearLayout::horizontal()
            .child(TextView::new(format!("{:2}", i + 1)).center().with_name(format!("ID {}", i)).fixed_width(4))
            .child(TextView::new(*joint_name).center().with_name(format!("Joint {}", i)).fixed_width(7))
            .child(TextView::new("----").center().with_name(format!("CurrPos {}", i)).fixed_width(8))
            .child(TextView::new("----").center().with_name(format!("CurrSpd {}", i)).fixed_width(8))
            .child(TextView::new("----").center().with_name(format!("Load {}", i)).fixed_width(8))
            .child(TextView::new("----").center().with_name(format!("Torque {}", i)).fixed_width(8))
            .child(TextView::new("----").center().with_name(format!("Volt {}", i)).fixed_width(6))
            .child(TextView::new("----").center().with_name(format!("Temp {}", i)).fixed_width(6))
            .child(TextView::new("----").center().with_name(format!("Curr {}", i)).fixed_width(6))
            .child(TextView::new("----").center().with_name(format!("Status {}", i)).fixed_width(8))
        .child(TextView::new("----").center().with_name(format!("TorqLim {}", i)).fixed_width(8));

            // .child(TextView::new("----").center().with_name(format!("Async {}", i)).fixed_width(6))
            // .child(TextView::new("----").center().with_name(format!("Lock {}", i)).fixed_width(6));
        layout.add_child(row.with_name(format!("servo_row_{}", i)));
    }

    // Add a dummy view to push the task count to the bottom
    layout.add_child(DummyView.full_height());

    // Add task run count at the bottom
    layout.add_child(
        Panel::new(
            LinearLayout::horizontal()
                .child(DummyView)
                .child(
                    LinearLayout::vertical()
                        .child(TextView::new("Task Run Count: 0").with_name("Task Count"))
                        .child(TextView::new("Last Update: N/A").with_name("Last Update"))
                        .child(TextView::new("Servo polling rate: N/A").with_name("Servo polling rate"))
                )
                .child(DummyView.fixed_width(2))
                .child(
                    LinearLayout::vertical()
                        .child(TextView::new("Min Angle: ----").with_name("MinAngle"))
                        .child(TextView::new("Max Angle: ----").with_name("MaxAngle"))
                        .child(TextView::new("Offset: ----").with_name("Offset"))
                )
                .child(DummyView.fixed_width(2))
                .child(
                    LinearLayout::vertical()
                        .child(TextView::new("Angle Range: ----°").with_name("AngleRange"))
                )
        )
        .title("Statistics")
        .full_width()
    );

    // Add instructions
    layout.add_child(
        TextView::new("Press 'H' for help")
            .center()
            .full_width()
    );

    layout.add_child(TextView::new("Calibration Pos: ----").with_name("CalibrationPos"));

    siv.add_fullscreen_layer(layout);

    // Set up a timer to update the UI
    siv.set_fps(30);

    // Clone Arc for the callback
    let servo_clone = Arc::clone(&servo);

    // Add a variable to keep track of the selected servo
    let selected_servo = Arc::new(Mutex::new(0));

    // Add variables for last update time and task count
    let last_update_time = Arc::new(Mutex::new(Instant::now()));

    siv.add_global_callback('q', |s| s.quit());

    // Modify Up and Down callbacks to wrap around
    let servo_clone_up = Arc::clone(&servo);
    let selected_servo_up = Arc::clone(&selected_servo);
    siv.add_global_callback(cursive::event::Event::Key(cursive::event::Key::Up), move |s| {
        let mut selected = selected_servo_up.lock().unwrap();
        *selected = (*selected + MAX_SERVOS - 1) % MAX_SERVOS;
        update_selected_row(s, *selected);
        update_angle_limits(s, *selected as u8 + 1, &servo_clone_up);
    });
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

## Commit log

2024-09-11 [ImgBot] Optimize images
    *Total -- 9,696.22kb -> 8,397.83kb (13.39%)
    /public/CAD.png -- 465.40kb -> 323.03kb (30.59%)
    /public/hackathon_team_2.png -- 2,114.75kb -> 1,654.93kb (21.74%)
    /public/waving.png -- 3,909.58kb -> 3,463.94kb (11.4%)
    /public/hackathon_team_1.png -- 3,206.50kb -> 2,955.94kb (7.81%)
2024-09-15 usb hid driver for hiwonder lsbc v1.6 board
2024-09-26 joints states/commands
2024-10-01 Bug fixes in robot.rs (legs/arms config holds hashmap
2024-10-01 Added print config helper to Robot
2024-10-01 Added config printing in main
2024-10-01 Improved robot-config-related structs and printing. Pub-ed the structs
2024-10-01 Added printing for debugging
2024-10-01 simplified bugged model.rs, added handwritten controller
    [controller.rs, main.rs]
2024-10-01 Switched to using candle_onnx for onnx reading
2024-10-01 Set up ML and PID controllers in controller.rs
2024-10-01 Switched to random actions from 0s
2024-10-03 forgot to add actual build stage lol
2024-10-03 WIP: servo control from rust
2024-10-03 Added missing servo lib path
2024-10-03 added calibration script as an artifact
2024-10-03 Calibration and servo utils
2024-10-03 update bom
2024-10-03 Added prefixes to calibration binaries
2024-10-03 Added setting/getting PID for servos; some refactoring
2024-10-04 Sort of working calibration script; ci files; cool table updates
2024-10-05 Manual calibration WIP
2024-10-06 Manual calibration
2024-10-06 Calibration notes
2024-10-06 Updated BOM
2024-10-06 Added servo error highlighting
    [hal.rs, sts_multitool.rs]
2024-10-08 servo reading WIP
2024-10-08 Revert "servo reading WIP"
    This reverts commit 5b2dc620533a9e16b20ff526634602d0b4a629aa.
    [controller.rs]
2024-10-11 update servo test build
2024-10-11 Validate that the limits were written & are correct
    [sts_multitool.rs]
2024-10-12 IMU HAL + demo
2024-10-12 Added deps for IMU
2024-10-16 Added i2cdev back
2024-10-16 Servo/python api implementation using websockets
2024-10-22 WIP calibration; milkv serialization by efuse data
2024-10-22 pybullet v1
    [Left_Hand.stl, Torso.stl, ankle_pitch_left.stl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]
2024-10-22 Calibration API
2024-10-23 Absoulte paths for camera binaries
2024-10-23 Correct library path for start from rc.d
    [sts_server.rs]
2024-10-24 Added torque control, fixed speeds, added speeds blabla
    [sts_server.rs]
2024-10-24 fix inference vecloity, position, and calibration
2024-10-24 reverse joints list for joint id mathcing
2024-10-24 servo offsets
2024-10-29 imu protocol update
2024-10-29 added imu api for gRPC
2024-10-29 imu build fix
2024-10-30 imu protocol rework
2024-11-02 direct imu
2024-11-03 spamming servos with continuous writes, customizable current threshold for calibration, moving one servo
2024-11-03 added missing fns for servos
    [sts3215.c]
2024-11-08 Made imu optional
2024-11-08 calibration failsafes, fixed scan
    [sts_server.rs]
2024-11-10 Micro Walking Hack (#47)
    * 50HZ inference
    * set two times for more stable behaviour
    * many fixes
    * IMU
    * add requirements
    * dashboard MVP
    * inline docs
    * improve graph
    * fix dashboard offset
    * refactor
    * fix inference HZ
    training is 100HZ, not 50HZ!
    * states v2
    * wave with legs
    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
    [imu.py, model.py, plot.py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]
2024-11-13 sts3215 current multiplier
